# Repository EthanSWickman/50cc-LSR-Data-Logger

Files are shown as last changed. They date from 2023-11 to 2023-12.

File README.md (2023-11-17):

# 50CC LSR Data Logger 

This repository is the home of data logger development for the 50cc Land Speed Record Motorcycle Racing Team at Oregon State University .

## Project Structure 
- /project/ - code base (we use C and CMake) - loosely follows https://cliutils.gitlab.io/modern-cmake/chapters/basics/structure.html
    - /project/apps - files to be compiled into executables
    - /project/src - library implementation files
    - /project/include - library header files
    - /project/build - build directory, contains binaries
    - /project/scripts - build/deploy scripts
    - /project/docs - documentation
    - /project/docs/schematic/ - wiring schematics 
- /examples/ - example cmake projects that exhibit important features of cmake and pico programming in C
- /notes/ - important notes for the datalogging team to reference

## Git Etiquette
- make a branch for new development, keep master clean, compileable, and in sync with the latest wiring diagram
- make targeted commits with meaningful messages

## Attributions
- uses carlk3's SD card interface library: https://github.com/carlk3/no-OS-FatFS-SD-SPI-RPi-Pico (following https://www.digikey.com/en/maker/projects/raspberry-pi-pico-rp2040-sd-card-example-with-micropython-and-cc/e472c7f578734bfd96d437e68e670050)

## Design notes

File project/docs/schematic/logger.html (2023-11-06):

# logger

## Diagram

## Bill of Materials

Id | Description | Qty | Unit | Designators
1 | Cable, 10 x 28 AWG | 0 | m | Data
2 | Cable, 3 x 28 AWG | 0 | m | 12V Power Wire, 5V Power Wire
3 | Cable, 6 x 28 AWG | 0 | m | Cowbell
4 | Cable, 8 x 28 AWG | 0 | m | 3V Power Wire
5 | Connector, ground, female, 7 pins | 1 | | Ground Rail
6 | Connector, headers, 2 pins | 1 | | Cowbell PCF8523 Clock
7 | Connector, headers, 4 pins | 1 | | Cowbell Micro SD Card Holder
8 | Connector, headers, draws 1.5ma, 6 pins | 3 | | MAX31855_coolant, MAX31855_coolant2, MAX31855_egt
9 | Connector, headers, male, 2 pins | 2 | | 12V Rail, 12V Source
10 | Connector, headers, male, 3 pins | 2 | | 12V to 5V Converter, Hall Effect Sensor
11 | Connector, headers, male, 41 pins | 1 | | Pico
12 | Connector, power, female, 2 pins | 1 | | 5V Rail
13 | Connector, power, female, 5 pins | 1 | | 3V Rail

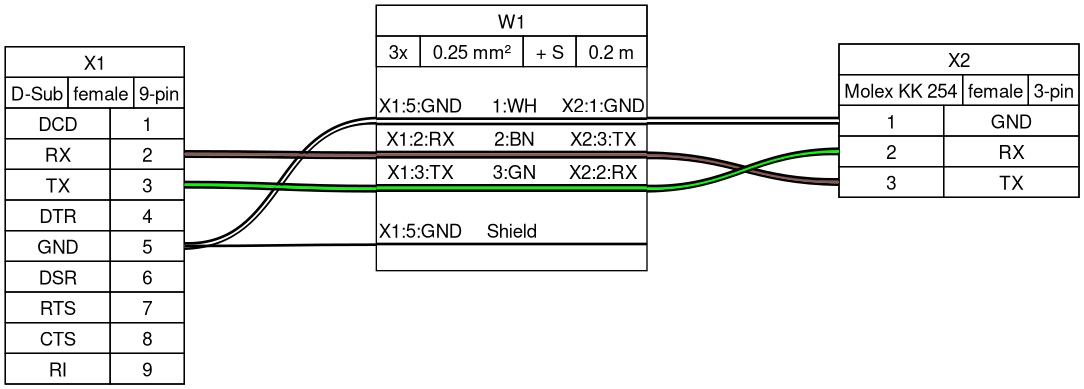
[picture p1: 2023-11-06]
project/docs/schematic/example/schematic.png

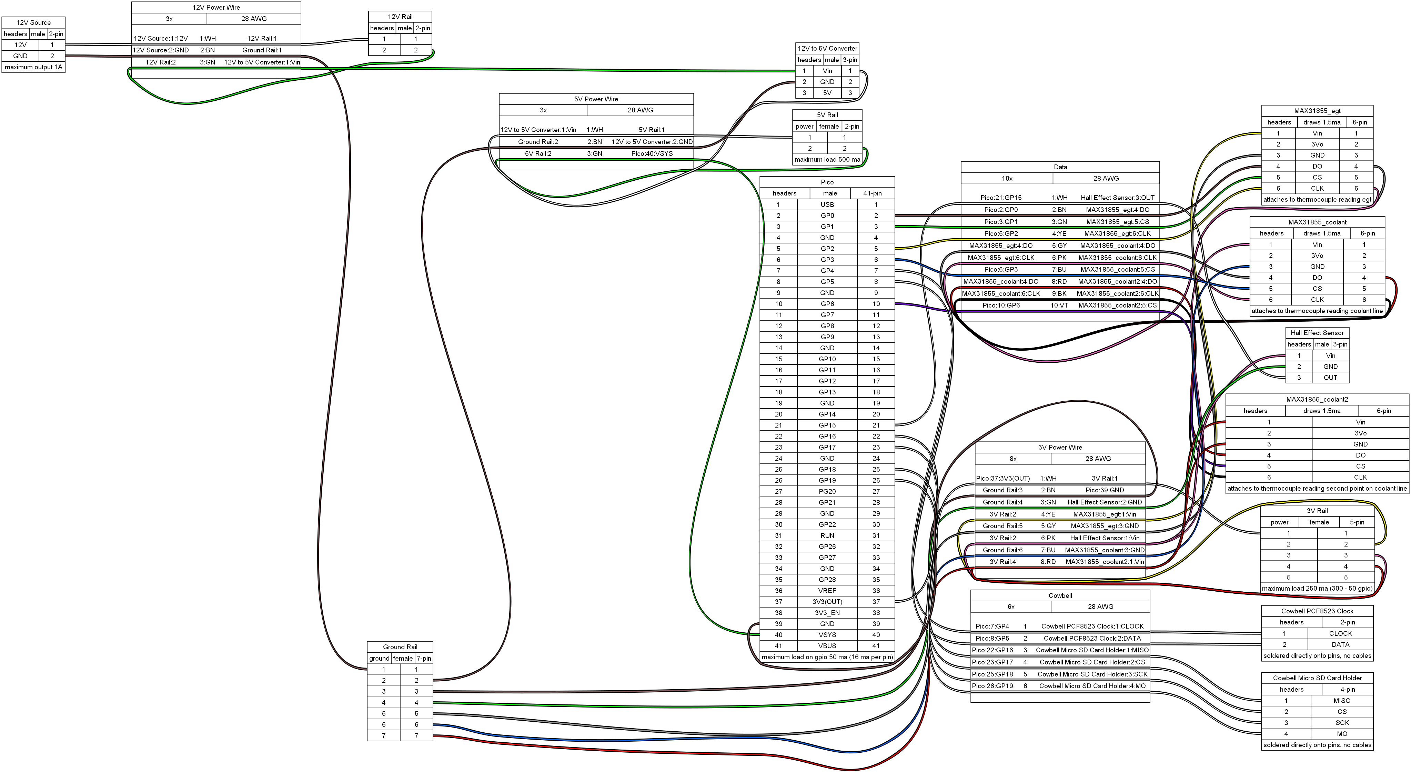
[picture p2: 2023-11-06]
project/docs/schematic/logger.png

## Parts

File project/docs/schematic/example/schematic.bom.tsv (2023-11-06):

Id | Description | Qty | Unit | Designators
1 | Cable, 3 x 0.25 mm² shielded | 0.2 | m | W1
2 | Connector, D-Sub, female, 9 pins | 1 |  | X1
3 | Connector, Molex KK 254, female, 3 pins | 1 |  | X2

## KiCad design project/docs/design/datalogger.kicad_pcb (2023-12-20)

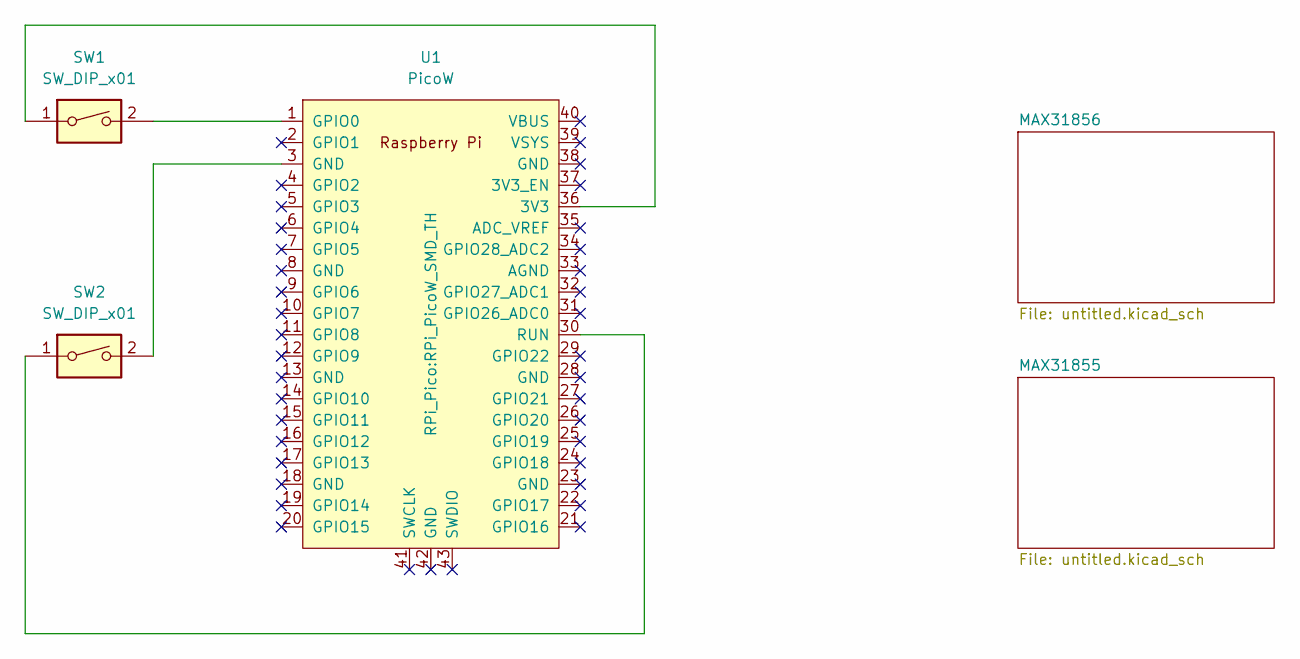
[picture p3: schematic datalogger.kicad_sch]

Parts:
SW1, SW2: SW_DIP_x01
U1: PicoW; RPi_PicoW_SMD_TH

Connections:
unnamed: SW1.1, U1.36 (3V3)
unnamed: SW1.2, U1.1 (GPIO0)
unnamed: SW2.1, U1.30 (RUN)
unnamed: SW2.2, U1.3 (GND)

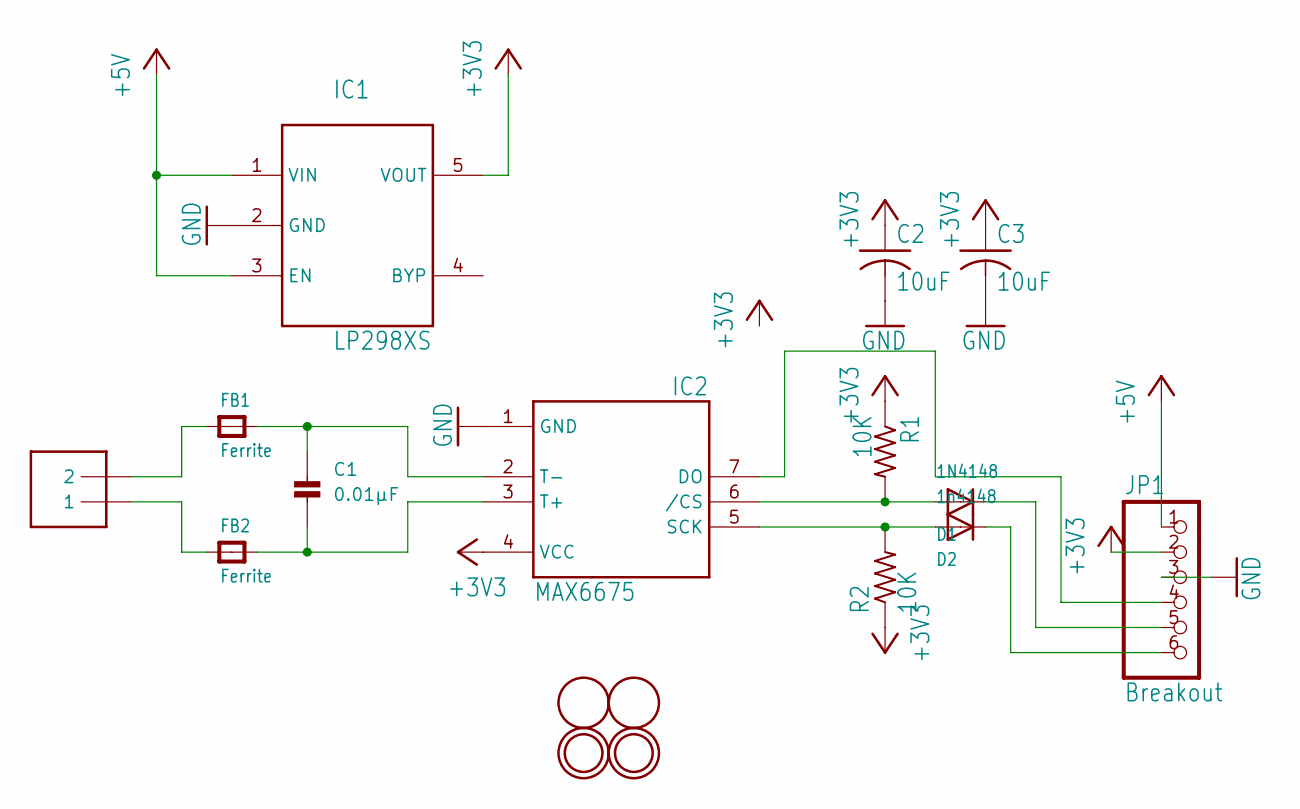
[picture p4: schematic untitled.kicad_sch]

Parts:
C1: 0.01µF; _0805
C2, C3: 10uF; C0805K
D1: 1N4148; SOD-323F
D2: 1n4148; SOD-323F
FB1, FB2: Ferrite; _0805
IC1: LP298XS; SOT23-5L
IC2: MAX6675; SO08
J1: 1X2-3.5MM
JP1: Breakout; 1X06_ROUND_76
R1, R2: 10K; R0805
U$1, U$3: FIDUCIAL; FIDUCIAL_1MM
U$2, U$4: MOUNTINGHOLE2.0; MOUNTINGHOLE_2.0_PLATED

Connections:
+3V3: C2.1, C3.1, IC1.5 (VOUT), IC2.4 (VCC), JP1.2, R1.1, R2.1
+5V: IC1.1 (VIN), IC1.3 (EN), JP1.1
GND: C2.2, C3.2, IC1.2 (GND), IC2.1 (GND), JP1.3
unnamed: C1.1, FB1.2, IC2.2 (T-)
unnamed: C1.2, FB2.2, IC2.3 (T+)
unnamed: D1.C, JP1.5
unnamed: D2.C, JP1.6
unnamed: FB1.1, J1.2
unnamed: FB2.1, J1.1
unnamed: IC2.7 (DO), JP1.4
unnamed: D2.A, IC2.5 (SCK), R2.2
unnamed: D1.A, IC2.6 (/CS), R1.2

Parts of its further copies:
U$5: MOUNTINGHOLE2.0; MOUNTINGHOLE_2.0_PLATED

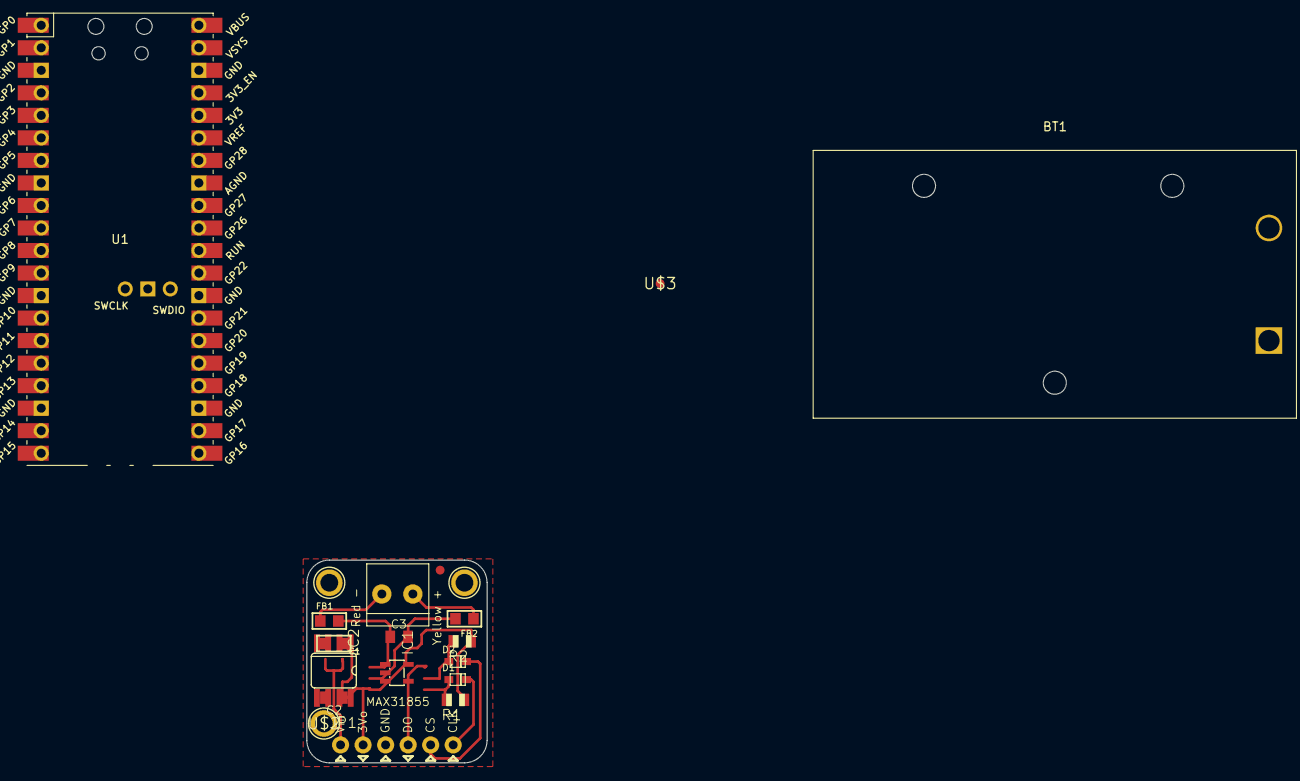
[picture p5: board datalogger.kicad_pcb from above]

Board: 2 copper layers, 20.3 x 22.9 mm, 21 parts (1 on the bottom side), 12 nets.

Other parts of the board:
BT1: Battery; BatteryHolder_Eagle_12BH611-GR
U$6: ADAFRUIT_3.5MM

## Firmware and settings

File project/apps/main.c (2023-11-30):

#include <stdio.h>
#include <stdlib.h>

#include "pico/stdlib.h"
#include "pico/cyw43_arch.h"
#include "pico/binary_info.h"
#include "hardware/i2c.h"
#include "pico/multicore.h"

#include "picowbell_pcf8520.h"
#include "picowbell_sd_card.h"
#include "writebuffer.h"
#include "pin_config.h"

auto_init_mutex(my_mutex);

const uint HZ = 50; // logs per second (keep under 50 until we solve high frequency problems!)
const uint64_t DELTA_T = 1000000 / HZ;
const uint SAVE_INTERVAL = 256; // should be 2^n for some integer n, represents how many logs until we save results to sd card

void core1_entry() {
    // init sd card
    FATFS fs;
    picowbell_sd_card_init(&fs);

    // open new log file
    FIL f;
    picowbell_sd_card_new_log(&f, 0);

    // receive writebuffer address for string communication between cores
    struct writebuffer* wb = (struct writebuffer*) multicore_fifo_pop_blocking();

    // forever write strings from core 0 to sd card
    uint i = 0;
    while (true) {
        // protect writebuffer access
        mutex_enter_blocking(&my_mutex);
        char* wb_out = writebuffer_out(wb);
        mutex_exit(&my_mutex);

        // continue if no logs to write
        if (wb_out == NULL) {
            continue;
        }

        // write logs
        else {
            f_printf(&f, "%s\n", wb_out);

            // sync sd card every SAVE_INTERVAL logs
            if ((i++ & (SAVE_INTERVAL - 1)) == 0) {
                f_sync(&f);
            }
        }
    }
}

int main() {
    // init stdio
    stdio_init_all();

    // init cyw43 
    if (cyw43_arch_init()) {
        printf("wifi init failed\n");
        return -1;
    }

    cyw43_arch_gpio_put(CYW43_WL_GPIO_LED_PIN, 1);

    gpio_init(LOG_START_BUTTON_PIN);
    gpio_set_dir(LOG_START_BUTTON_PIN, GPIO_IN);
    while (gpio_get(LOG_START_BUTTON_PIN) != 1) {
        continue;
    }

    // launch core 1
    multicore_launch_core1(core1_entry);
   
    // init pcf8520 clock
    picowbell_pcf8520_init();

    // light up the logging indicator
    cyw43_arch_gpio_put(CYW43_WL_GPIO_LED_PIN, 1);
    
    // get current time
    datetime_t t = picowbell_pcf8520_get_time();

    // initialize writebuffer for cross-core communication
    struct writebuffer wb;
    wb.in = wb.out = 0;

    // push writebuffer address to core 1
    multicore_fifo_push_blocking((uintptr_t) &wb);

    // start logs
    sleep_ms(1000);
    printf("starting logs...\n");

    // main logging loop
    while (true) {
        // wait until next second
        picowbell_pcf8520_wait_next_second(&t);

        // send a log string to core 1 every DELTA_T microseconds  
        absolute_time_t log_time = get_absolute_time();
        for (uint i = 0; i < HZ; i++) {
            // flash led for 1st half of second
            if (i > (HZ / 2)) cyw43_arch_gpio_put(CYW43_WL_GPIO_LED_PIN, 1);

            // protect writebuffer access 
            mutex_enter_blocking(&my_mutex);
            char* wb_in = writebuffer_in(&wb);
            mutex_exit(&my_mutex);

            // if buffer is full, print error
            if (wb_in == NULL) {
                printf("core 0: full buffer!\n");
            }

            // write to buffer
            else {
                sprintf(wb_in, "%02d/%02d/%02d-%02d:%02d:%02d", t.month, t.day, t.year, t.hour, t.min, t.sec);
            }

            // sleep until time to write next log
            log_time = delayed_by_us(log_time, DELTA_T);
            sleep_until(log_time);
        }

        // turn led off
        cyw43_arch_gpio_put(CYW43_WL_GPIO_LED_PIN, 0);
    }

    return 0;
}

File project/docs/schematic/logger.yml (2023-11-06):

connectors: 
  # power sources/rails
  12V Source: 
    type: headers
    subtype: male
    pinlabels: [12V, GND]
    notes: maximum output 1A
  12V Rail: 
    type: headers
    subtype: male
    pincount: 2
  5V Rail: 
    type: power
    subtype: female 
    pincount: 2
    notes: maximum load 500 ma
  3V Rail: 
    type: power
    subtype: female
    pincount: 5
    notes: maximum load 250 ma (300 - 50 gpio)
  Ground Rail:
    type: ground
    subtype: female
    pincount: 7

  # misc
  12V to 5V Converter: 
    type: headers
    subtype: male
    pinlabels: [Vin, GND, 5V]

  # pico
  Pico:
    type: headers
    subtype: male
    pinlabels: [USB, GP0, GP1, GND, GP2, GP3, GP4, GP5, GND, GP6, GP7, GP8, GP9, GND, GP10, GP11, GP12, GP13, GND, GP14, GP15, GP16, GP17, GND, GP18, GP19, PG20, GP21, GND, GP22, RUN, GP26, GP27, GND, GP28, VREF, 3V3(OUT), 3V3_EN, GND, VSYS, VBUS]
    notes: maximum load on gpio 50 ma (16 ma per pin)

  # sensors
  Cowbell PCF8523 Clock:
    type: headers
    pinlabels: [CLOCK, DATA]
    notes: soldered directly onto pins, no cables
  Cowbell Micro SD Card Holder:
    type: headers
    pinlabels: [MISO, CS, SCK, MO]
    notes: soldered directly onto pins, no cables
  MAX31855_egt: &templateMAX31855
    type: headers
    subtype: draws 1.5ma 
    pinlabels: [Vin, 3Vo, GND, DO, CS, CLK]
    notes: attaches to thermocouple reading egt 
  MAX31855_coolant:
    <<: *templateMAX31855
    notes: attaches to thermocouple reading coolant line
  MAX31855_coolant2:
    <<: *templateMAX31855
    notes: attaches to thermocouple reading second point on coolant line
  Hall Effect Sensor: 
    type: headers
    subtype: male
    pinlabels: [Vin, GND, OUT]

cables:
  # cables for data transmission
  Data: 
    gauge: 28 AWG
    wirecount: 10 
    color_code: DIN
  Cowbell:
    gauge: 28 AWG
    wirecount: 6 

  # power cables
  12V Power Wire:
    gauge: 28 AWG
    wirecount: 3 
    color_code: DIN
  5V Power Wire: 
    gauge: 28 AWG
    wirecount: 3
    color_code: DIN
  3V Power Wire:
    gauge: 28 AWG
    wirecount: 8 
    color_code: DIN
 
connections: 
  # 12V expansion to rail
  - 
    - 12V Source: [1]
    - 12V Power Wire: [1]
    - 12V Rail: [1]
  -
    - 12V Source: [2]
    - 12V Power Wire: [2]
    - Ground Rail: [1]

  # create 5V rail
  - 
    - 12V Rail: [2]
    - 12V Power Wire: [3]
    - 12V to 5V Converter: [1]
  - 
    - 12V to 5V Converter: [1]
    - 5V Power Wire: [1]
    - 5V Rail: [1]
  - 
    - Ground Rail: [2]
    - 5V Power Wire: [2]
    - 12V to 5V Converter: [2]

  # create 3V rail
  - 
    - Pico: [37]
    - 3V Power Wire: [1]
    - 3V Rail: [1]

  # 12V peripherals


  # 5V peripherals
  # pico
  -
    - 5V Rail: [2]
    - 5V Power Wire: [3]
    - Pico: [40]
  - 
    - Ground Rail: [3]
    - 3V Power Wire: [2]
    - Pico: [39]

  # 3V peripherals
  # PCF8523 clock
  - 
    - Pico: [7-8]
    - Cowbell: [1-2]
    - Cowbell PCF8523 Clock: [1-2]
  # micro-SD Card holder
  - 
    - Pico: [22-23, 25-26]
    - Cowbell: [3-6]
    - Cowbell Micro SD Card Holder: [1-4]
  # hall effect sensor
  -
    - 3V Rail: [2]
    - 3V Power Wire: [6]
    - Hall Effect Sensor: [1]
  - 
    - Ground Rail: [4]
    - 3V Power Wire: [3]
    - Hall Effect Sensor: [2]
  - 
    - Pico: [21]
    - Data: [1]
    - Hall Effect Sensor: [3]
  # egt temperature sensor
  - 
    - 3V Rail: [2]
    - 3V Power Wire: [4]
    - MAX31855_egt: [1]
  -
    - Ground Rail: [5]
    - 3V Power Wire: [5]
    - MAX31855_egt: [3]
  -
    - Pico: [2-3,5]
    - Data: [2-4]
    - MAX31855_egt: [4-6]
  # coolant temperature sensor
  - 
    - 3V Rail: [3]
    - 3V Power Wire: [6]
    - MAX31855_coolant: [1]
  -
    - Ground Rail: [6]
    - 3V Power Wire: [7]
    - MAX31855_coolant: [3]
  - 
    - MAX31855_egt: [4, 6]
    - Data: [5-6]
    - MAX31855_coolant: [4, 6]
  - 
    - Pico: [6]
    - Data: [7]
    - MAX31855_coolant: [5]
  # coolant2 temperature sensor
  - 
    - 3V Rail: [4]
    - 3V Power Wire: [8]
    - MAX31855_coolant2: [1]
  -
    - Ground Rail: [7]
    - 3V Power Wire: [8]
    - MAX31855_coolant2: [3]
  - 
    - MAX31855_coolant: [4, 6]
    - Data: [8-9]
    - MAX31855_coolant2: [4, 6]
  - 
    - Pico: [10]
    - Data: [10]
    - MAX31855_coolant2: [5]

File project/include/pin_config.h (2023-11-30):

#ifndef PIN_CONFIG_H
#define PIN_CONFIG_H

#include "pico/stdlib.h"

/*

This config file is for reserving pins. Take care to document your sensors

Pinout:

[0  - SPI0 RX  - I2C0 SDA - UART0 TX] -------- [Vbus]
[1  - SPI0 CSn - I2C0 SCL - UART0 RX] -------- [Vsys]
[GND] ---------------------------------------- [GND]
[2  - SPI0 SCK - I2C1 SDA] ------------------- [3V3_EN]
[3  - SPI0 TX  - I2C1 SCL] ------------------- [3V3(OUT)]
[4  - SPI0 RX  - I2C0 SDA - UART1 TX] -------- [ADC_VREF]
[5  - SPI0 CSn - I2C0 SCL - UART1 RX] -------- [28  - ADC2]
[GND] ---------------------------------------- [GND - AGND]
[6  - SPI0 SCK - I2C1 SDA] ------------------- [27  - ADC1     - I2C1 SCL]
[7  - SPI0 TX  - I2C1 SCL] ------------------- [26  - ADC0     - I2C1 SCL]
[8  - SPI1 RX  - I2C0 SDA - UART1 TX] -------- [RUN]
[9  - SPI1 CSn - I2C0 SCL - UART1 RX] -------- [22]
[GND] ---------------------------------------- [GND]
[10 - SPI1 SCK - I2C1 SDA] ------------------- [21  -          - I2C0 SCL]
[11 - SPI1 TX  - I2C1 SCL] ------------------- [20  -          - I2C0 SDA]
[12 - SPI1 RX  - I2C0 SDA - UART0 TX] -------- [19  - SPI0 TX  - I2C1 SCL]
[13 - SPI1 CSn - I2C0 SCL - UART0 RX] -------  [18  - SPI0 SCK - I2C1 SDA]
[GND] ---------------------------------------- [GND]
[14 - SPI1 SCK - I2C1 SDA] ------------------- [17  - SPI0 CSn - I2C0 SCL - UART0 RX]
[15 - SPI1 TX  - I2C1 SCL] ------------------- [16  - SPI0 RX  - I2C0 SDA - UART0 TX]


Controller Reservations (please avoid conflicts until necessary): 

SPI0: sd card
SPI1: 

I2C0: pcf8520 
I2C1: 

UART0:
UART1:

*/

#define LOG_START_BUTTON_PIN 0
//const uint PIN = 1;
//const uint PIN = 2;
//const uint PIN = 3;
#define PCF8520_SDA_PIN 4 // ADALOGGER IMPOSED
#define PCF8520_SCL_PIN 5 // ADALOGGER IMPOSED
//const uint PIN = 6;
//const uint PIN = 7;
//const uint PIN = 8;
//const uint PIN = 9;
//const uint PIN = 10;
//const uint PIN = 11;
//const uint PIN = 12;
//const uint PIN = 13;
//const uint PIN = 14;
//const uint PIN = 15;
#define SD_MISO_PIN 16 // ADALOGGER IMPOSED
#define SD_CS_PIN 17 // ADALOGGER IMPOSED
#define SD_SCK_PIN 18 // ADALOGGER IMPOSED
#define SD_MOSI_PIN 19 // ADALOGGER IMPOSED
//const uint PIN = 20;
//const uint PIN = 21;
//const uint PIN = 22;
//const uint PIN = 26;
//const uint PIN = 27;
//const uint PIN = 28;

#endif

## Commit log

2023-10-20 add example program using adc and pwm
2023-11-06 add basic wiring schematic
    [logger.bom.tsv, schematic.bom.tsv]
2023-11-06 add wiring color to schematic
    [logger.bom.tsv]
2023-11-06 add thermocouple boards to schematic'
    [logger.bom.tsv]
2023-11-06 add comments to schematic file
    [logger.bom.tsv]
2023-11-06 update schematic to use correct GPIOs
    [logger.bom.tsv]
2023-11-12 alter directory structure
    [logger.bom.tsv, schematic.bom.tsv]
2023-11-12 added clock library and reorganized directory structure
    [logger.bom.tsv, schematic.bom.tsv]
2023-11-14 Made led indicator keep led on constantly. Changed makelists.txt to work with it.
2023-11-17 moved pico sd card interface library
2023-11-23 add multicore logging, with awful bug that needs to be explored
    [main.c]
2023-11-23 one bug fixed, another begins, something is crashing with frequency > 200 hz ish
    [main.c]
2023-11-28 finish sd card writing w/ multicores up to 50hz logs
2023-11-28 re-adding pico sd card library
2023-11-30 add global pin configuration file
2023-12-20 start kicad diagram
    [datalogger.kicad_pcb, datalogger.kicad_sch, untitled.kicad_sch]
